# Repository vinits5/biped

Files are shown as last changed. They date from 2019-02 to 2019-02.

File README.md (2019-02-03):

# Biped Project

## Biped Assembly

It contains all the SolidWork parts for Biped Robot along with its Assembly.
<p float="center">
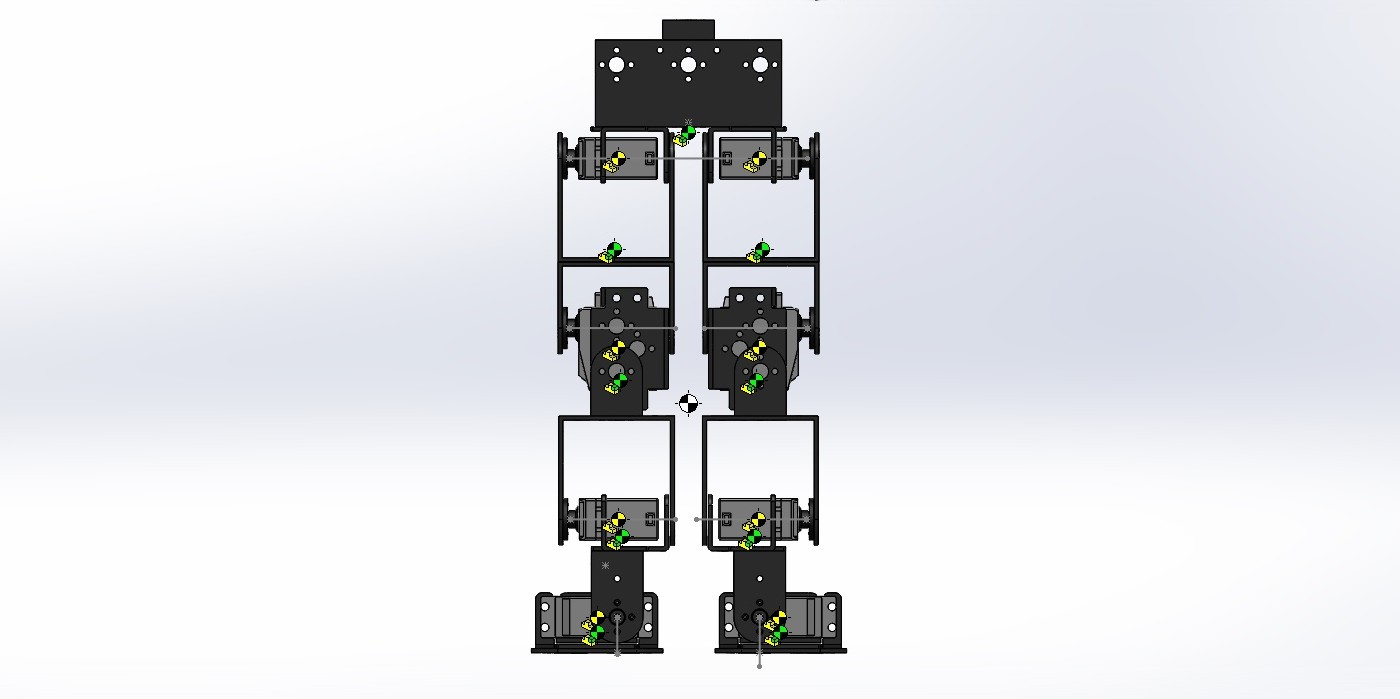
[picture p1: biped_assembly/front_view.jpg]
Front View of Assembly
	
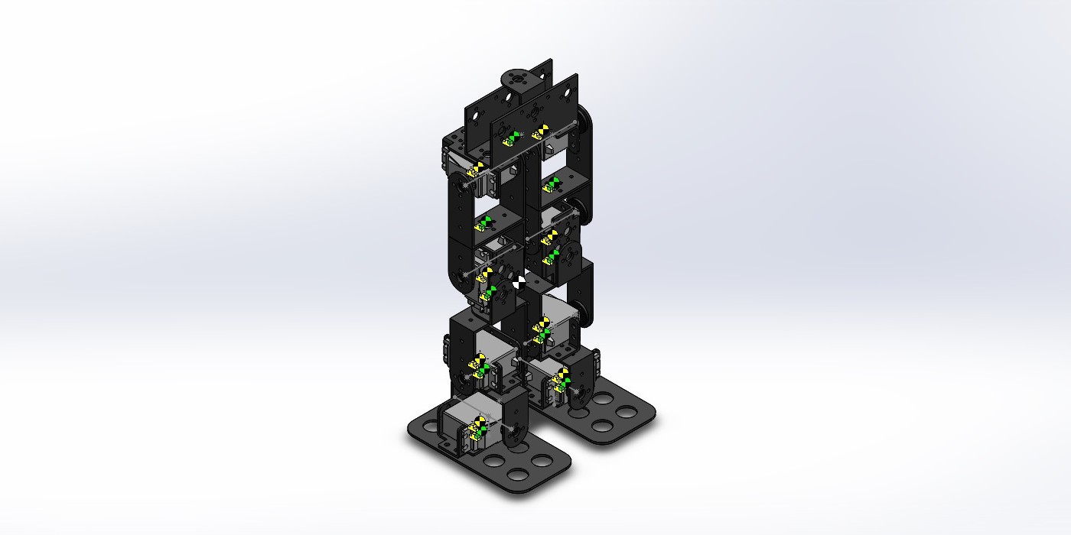
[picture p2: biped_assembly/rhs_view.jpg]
Right Hand Side View
	
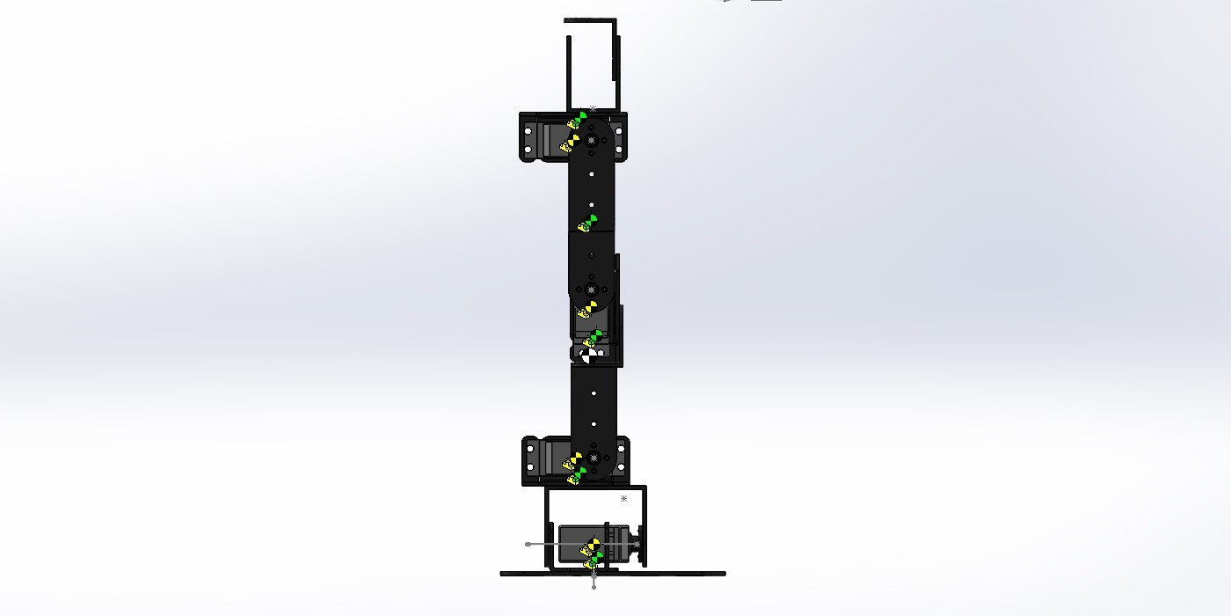
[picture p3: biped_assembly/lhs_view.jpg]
Left Hand Side View
	
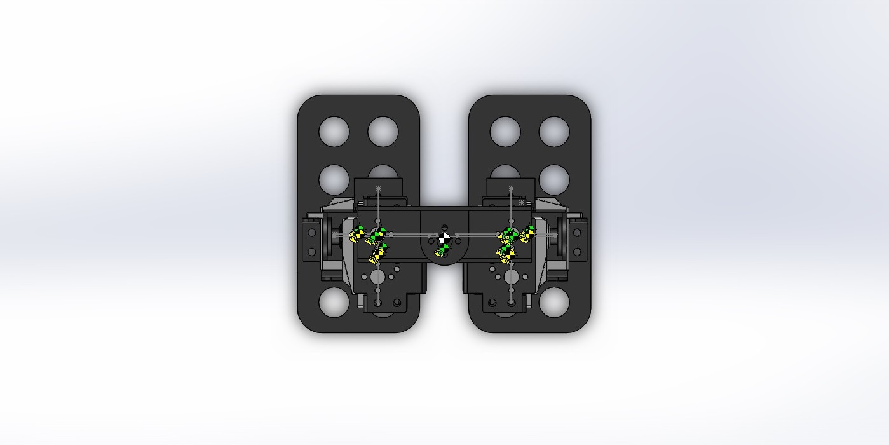
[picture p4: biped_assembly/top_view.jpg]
Top View
	
</p>

### Rendered Assembly
<p align="center">
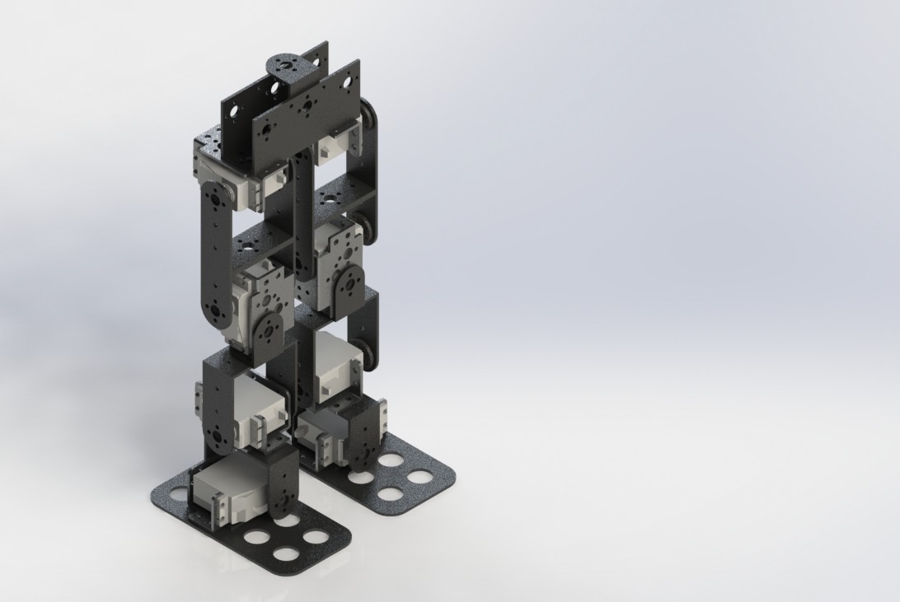
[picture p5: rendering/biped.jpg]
Rendered Biped
	
</p>

### Simulink Simulation
<p align="center">
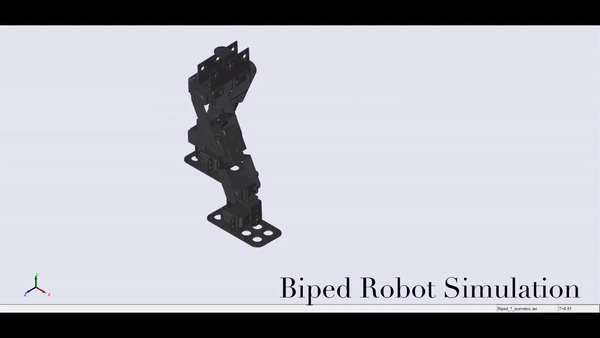
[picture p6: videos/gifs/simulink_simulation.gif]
	
</p>

## Robot

<p align="center">
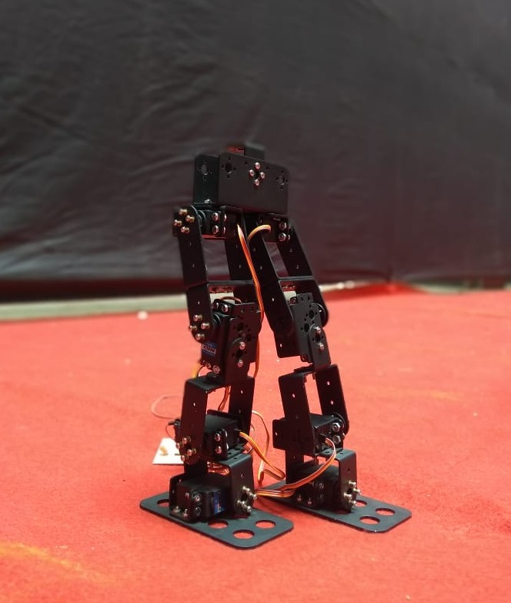
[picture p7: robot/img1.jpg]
	
</p>

<p align="center">
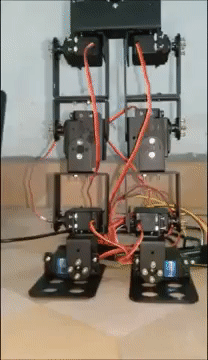
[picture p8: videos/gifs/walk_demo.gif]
	
</p>

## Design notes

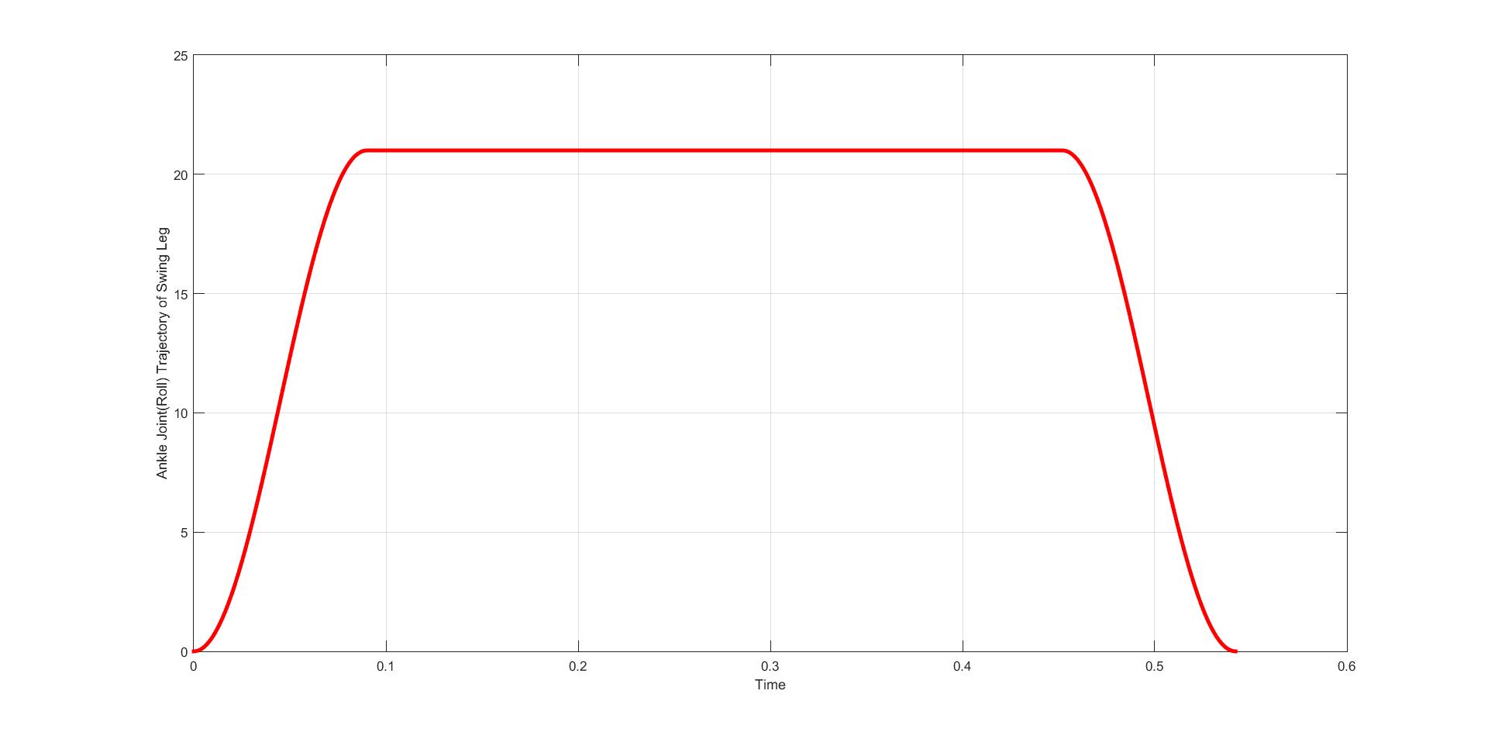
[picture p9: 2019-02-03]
biped_gait/Swing Ankle Roll.jpg

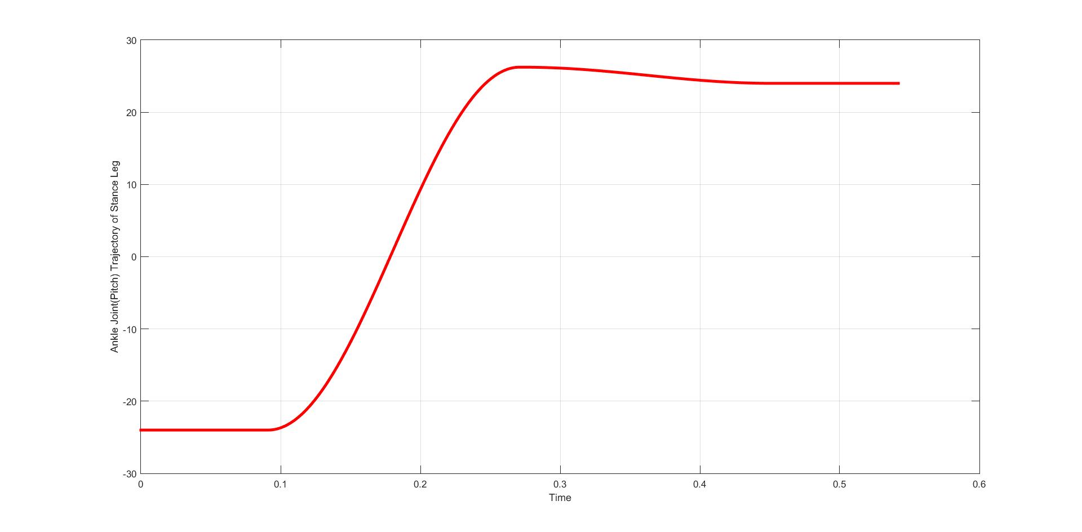
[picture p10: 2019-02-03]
biped_gait/Stance Ankle Pitch.jpg

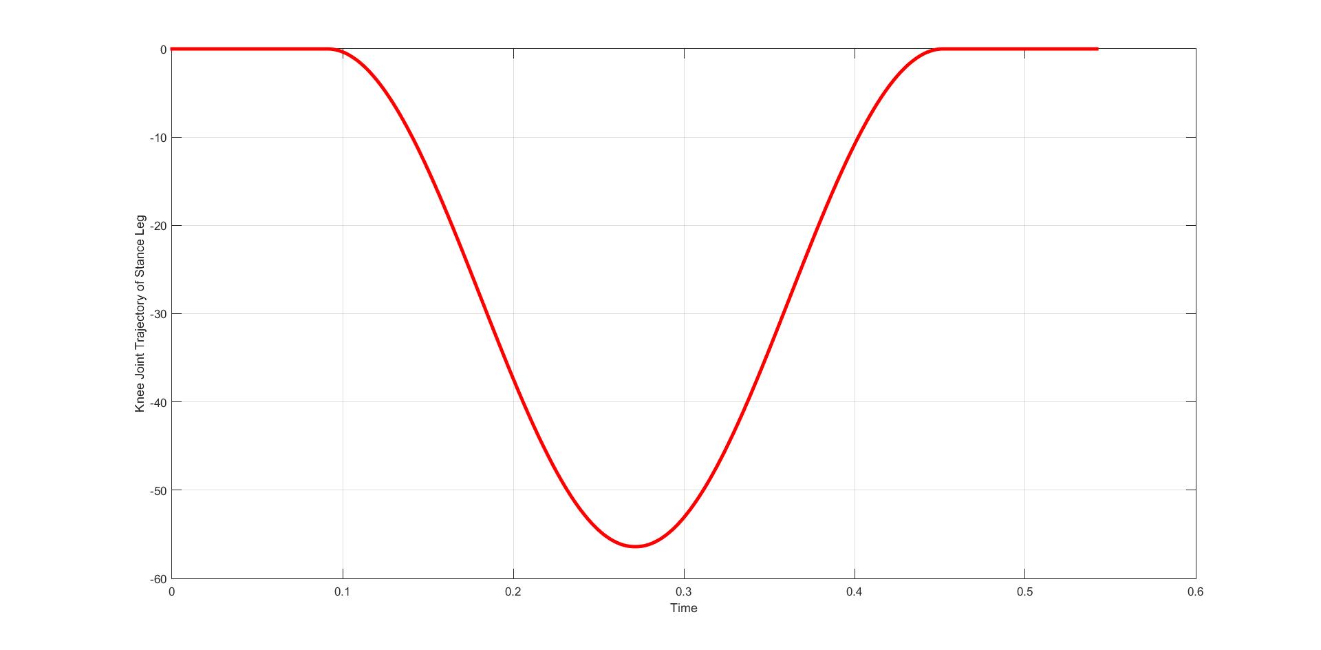
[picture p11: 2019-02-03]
biped_gait/Stance Knee.jpg

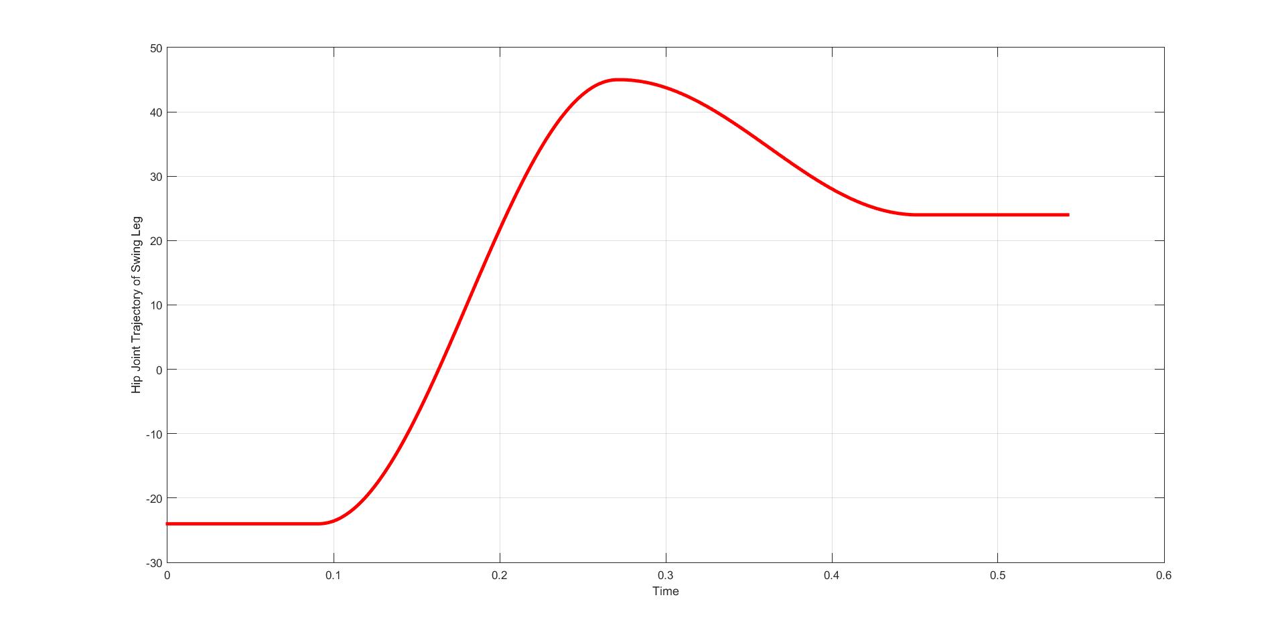
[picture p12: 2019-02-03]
biped_gait/Swing Hip.jpg

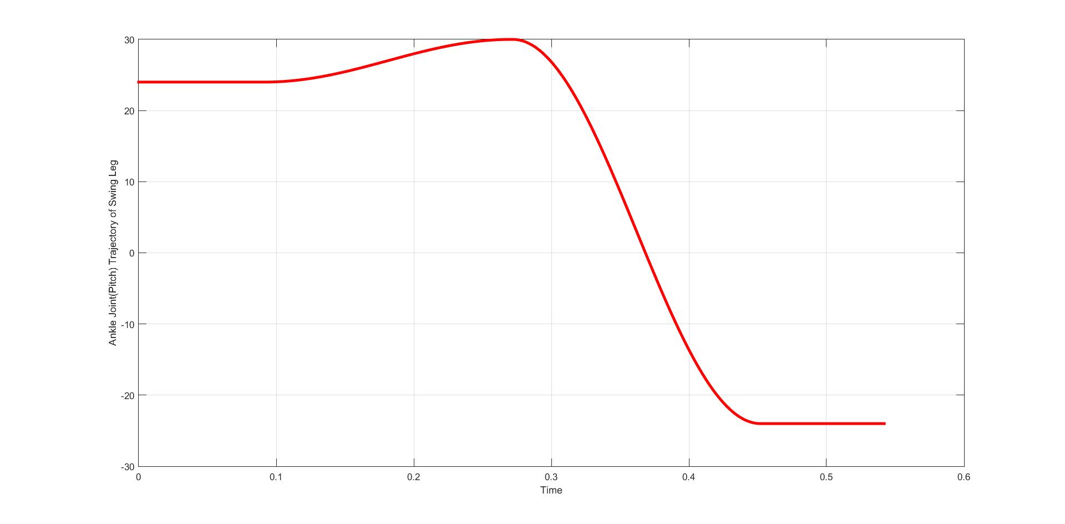
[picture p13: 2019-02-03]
biped_gait/Swing Ankle Pitch.jpg

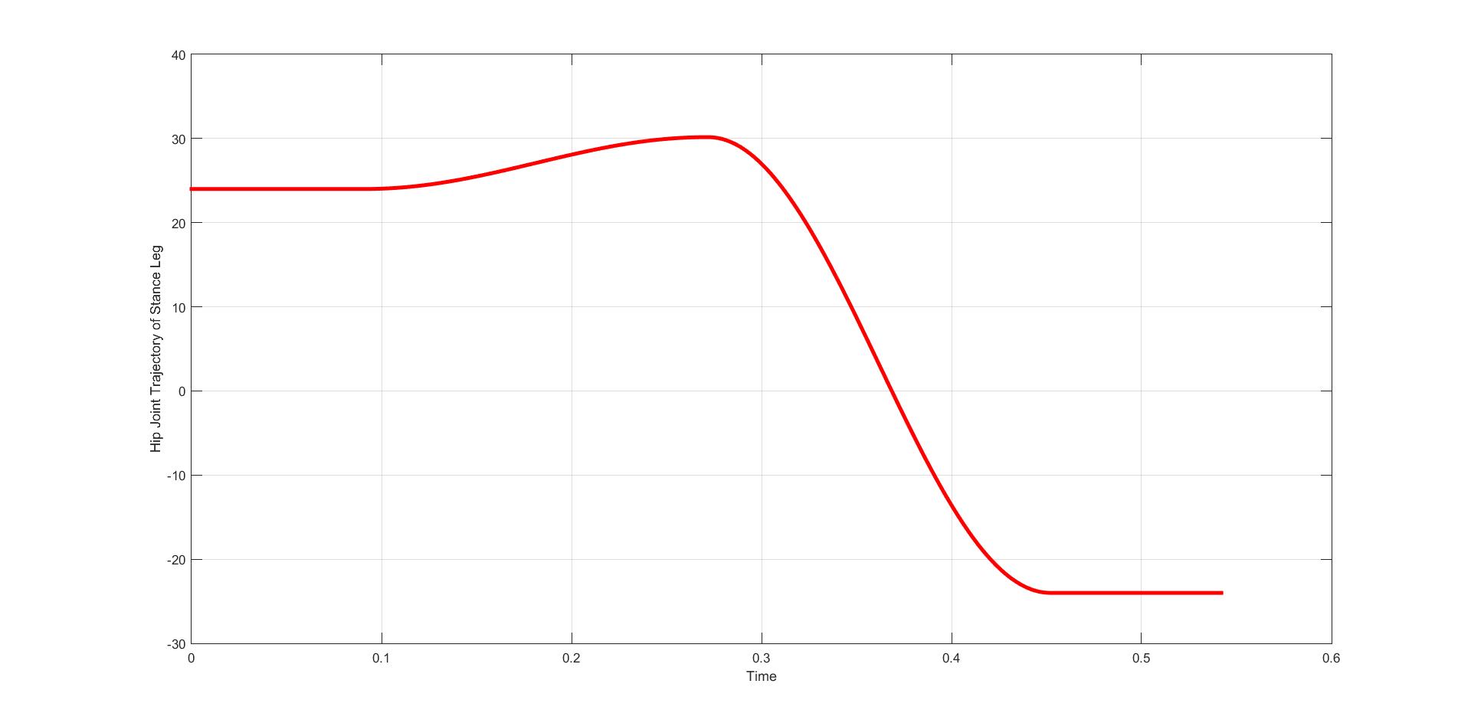
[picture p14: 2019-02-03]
biped_gait/Stance Hip.jpg

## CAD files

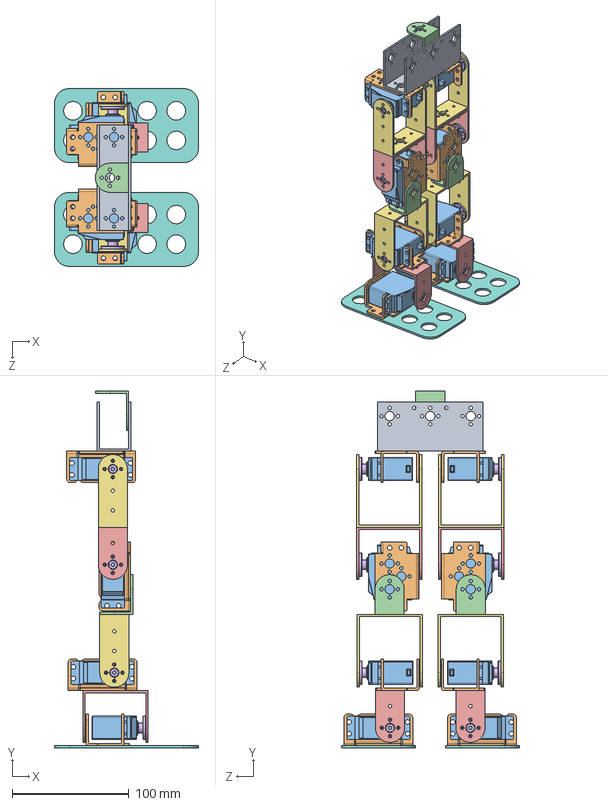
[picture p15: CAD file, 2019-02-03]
biped_assembly/Biped.SLDASM
123.4 x 305.8 x 152.4 mm
LARGE_U_BEAM_ALUMINIUM_SERVO_BRACKET
MULTIPURPOSE_Bracket x 8
Futaba_Servo_Motor x 8
L_SHAPED_INTERCONNECT_SERVO_BRACKET x 3
SHORT_U_SHAPE_ALUMINIUM_BRACKET x 4
Servo_Horn x 8
LONG_U_SHAPE_ALUMINIUM_BRACKET x 4
ROBOT_FEER_ALUMINIUM_SERVO_BRACKET x 2

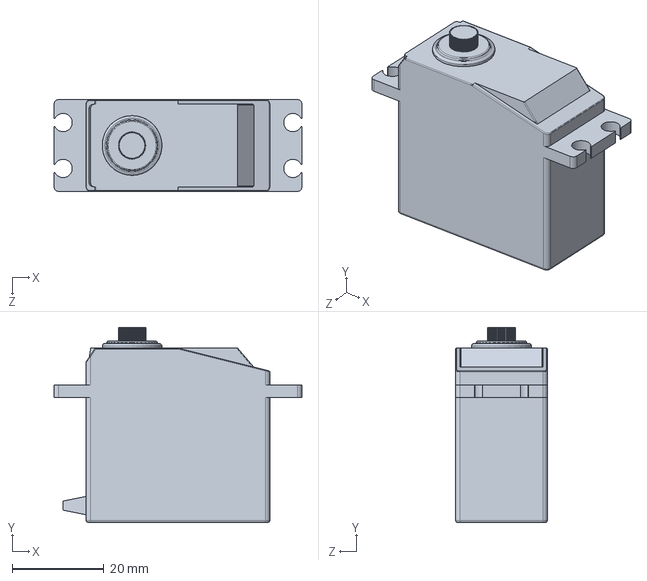
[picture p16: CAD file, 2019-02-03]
biped_assembly/Futaba_Servo_Motor.SLDPRT
54.0 x 42.5 x 20.0 mm

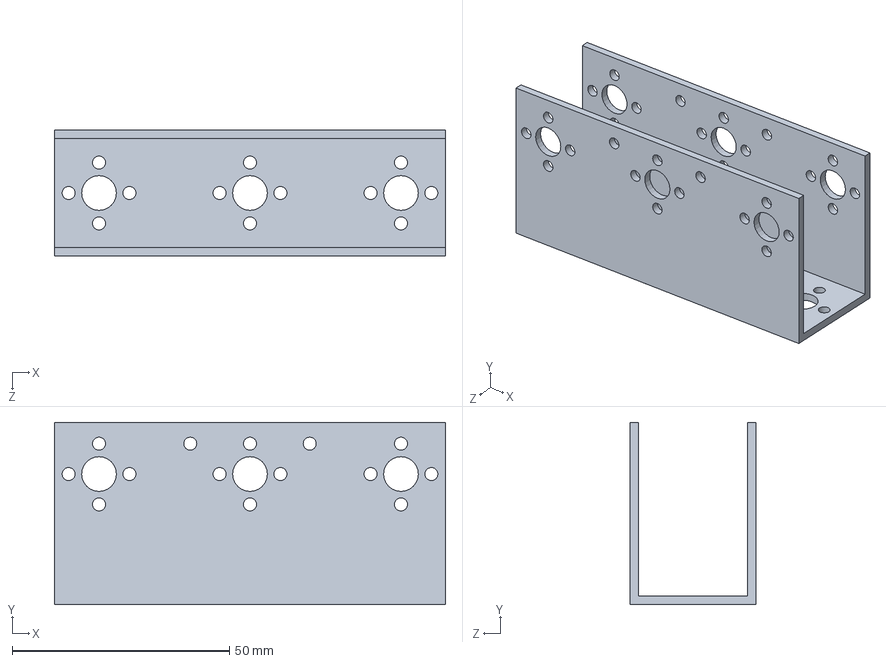
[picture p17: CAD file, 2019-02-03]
biped_assembly/LARGE_U_BEAM_ALUMINIUM_SERVO_BRACKET.SLDPRT
90.0 x 42.0 x 29.0 mm

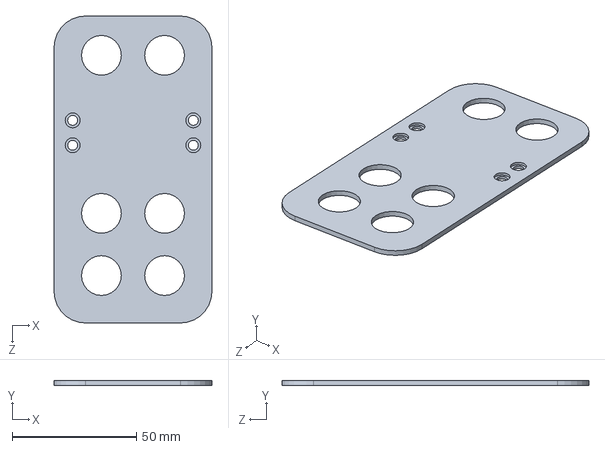
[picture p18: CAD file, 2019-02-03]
biped_assembly/ROBOT_FEER_ALUMINIUM_SERVO_BRACKET.SLDPRT
63.5 x 2.00 x 123.4 mm

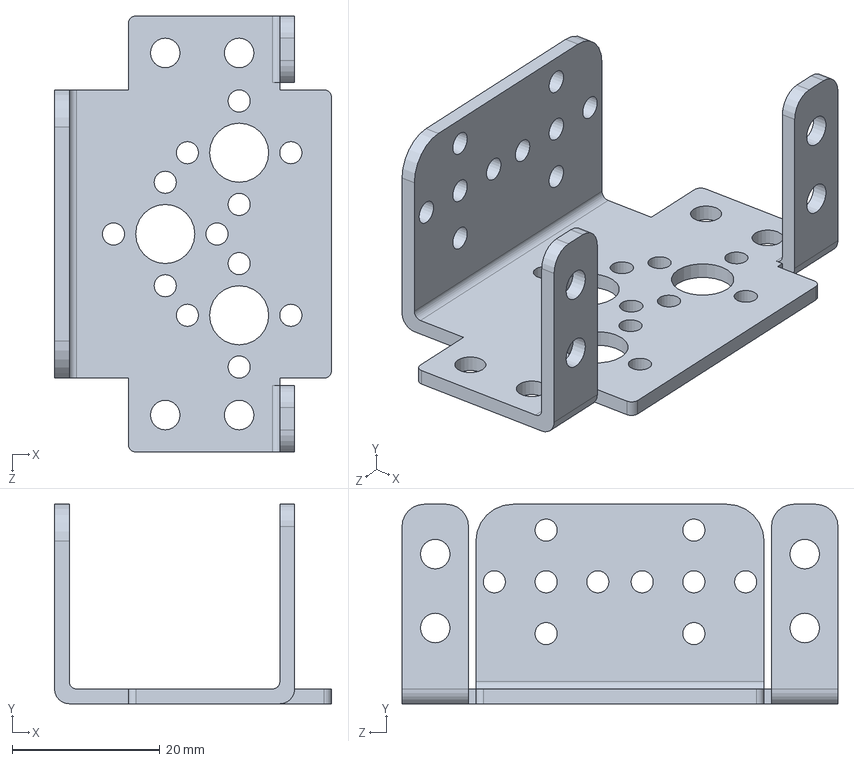
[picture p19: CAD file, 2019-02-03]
biped_assembly/MULTIPURPOSE_Bracket.SLDPRT
37.5 x 27.0 x 59.0 mm

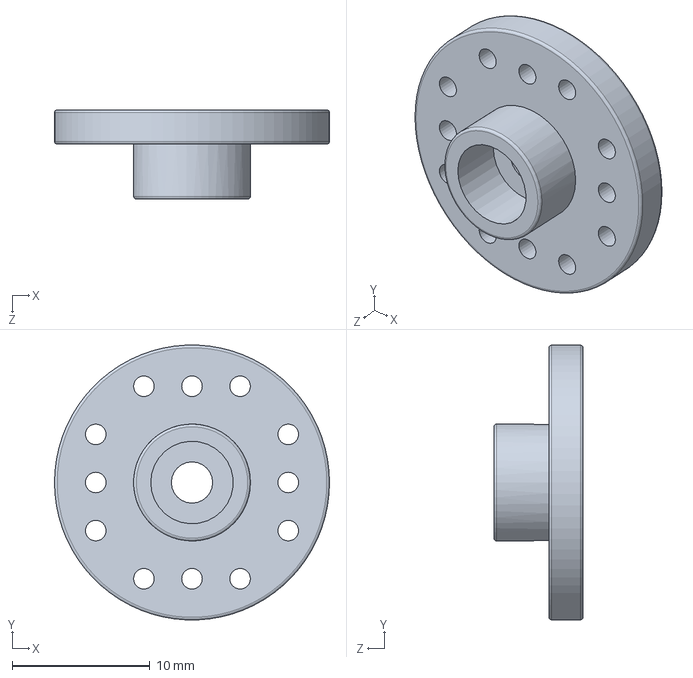
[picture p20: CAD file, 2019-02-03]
biped_assembly/Servo_Horn.SLDPRT
20.0 x 20.0 x 6.50 mm

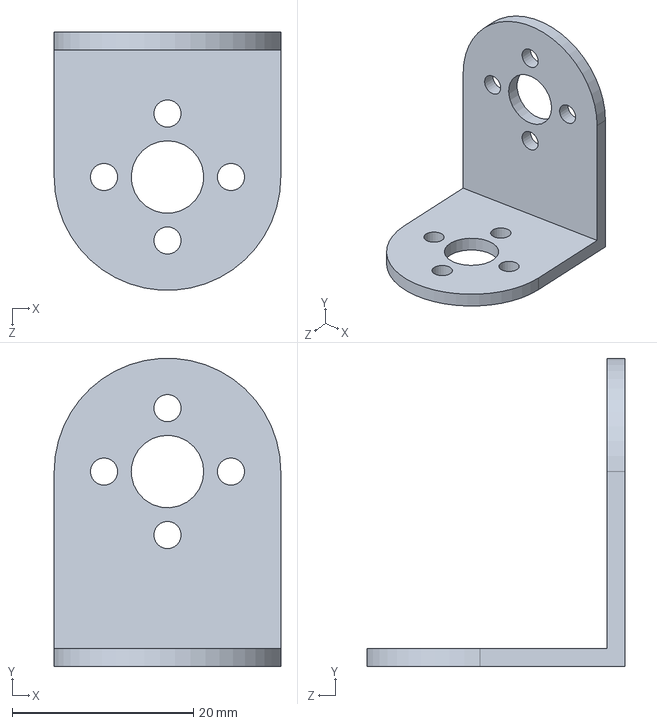
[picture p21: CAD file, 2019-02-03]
biped_assembly/L_SHAPED_INTERCONNECT_SERVO_BRACKET.SLDPRT
25.0 x 34.0 x 28.5 mm

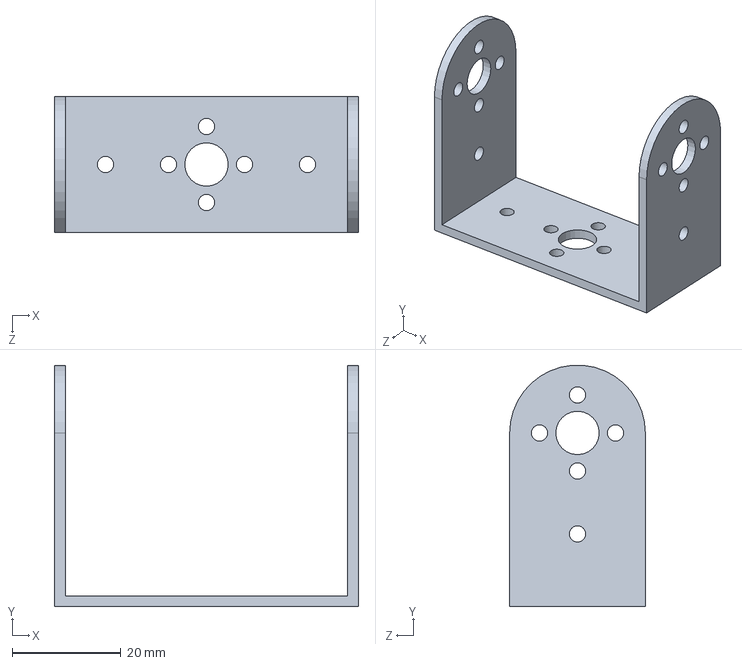
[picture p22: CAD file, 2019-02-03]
biped_assembly/SHORT_U_SHAPE_ALUMINIUM_BRACKET.SLDPRT
56.0 x 44.5 x 25.0 mm

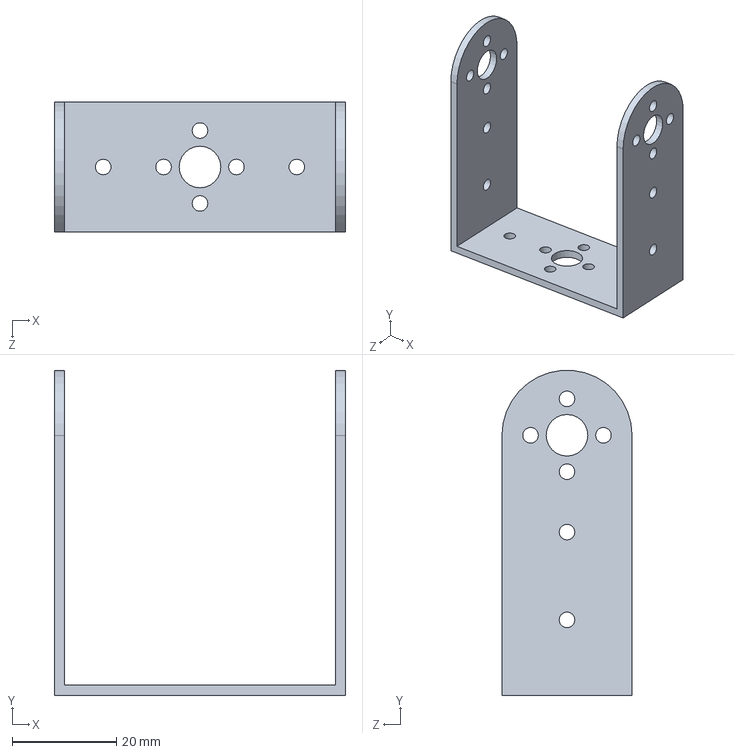
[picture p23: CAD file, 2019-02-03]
biped_assembly/LONG_U_SHAPE_ALUMINIUM_BRACKET.SLDPRT
56.0 x 62.4 x 25.0 mm

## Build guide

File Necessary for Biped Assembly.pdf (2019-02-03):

Created by Cytron Technologies Sdn. Bhd. – All Rights Reserved | 1

### OVERVIEW

This document describes the development of Cytron Technologies DIY (Do It Yourself) Project No.18 (PR18). This project will use PIC16F876A to communicate with Cytron SC16A servo controller to control the biped that built up with Cytron servo motors and servo brackets. It provides a LCD to display the information. Circuit schematic diagram and sample PIC source code are provided. Source code provides a simple biped walking program and servo position calibrating function.

PR18

### FEATURES

Basic Circuit
- PIC16F876A microcontroller
- Onboard 5V high current supply for SC16A
- Protection against overload (3A fuse)
- LCD screen display

SC16A Servo Controller
- Provides up to 16 control channels
- Simple communication protocol with UART

Biped
- 6 Cytron C40R servo motors
- 8 Cytron HD-SB-SH servo holders
- 6 Cytron U-Joints for servo motor

# Walking with Cytron Servo Motor

# Version 1.0

## August 2008

Cytron Technologies Sdn. Bhd.

Information contained in this publication regarding device applications and the like is intended through suggestion only and may be superseded by updates. It is your responsibility to ensure that your application meets with your specifications. No representation or warranty is given and no liability is assumed by Cytron Technologies Incorporated with respect to the accuracy or use of such information or infringement of patents or other intellectual property rights arising from such use or otherwise. Use of Cytron Technologies’s products as critical components in life support systems is not authorized except with express written approval by Cytron Technologies. No licenses are conveyed, implicitly or otherwise, under any intellectual property rights.

ROBOT . HEAD to TOE
PR18 – Walking With Cytron Servo Motor

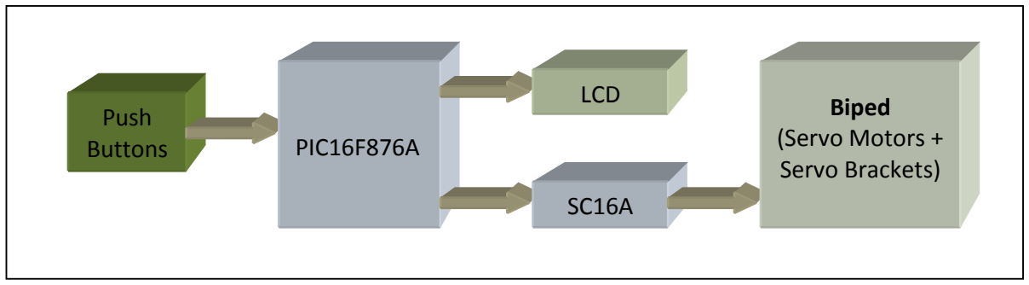
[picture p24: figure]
Push; Buttons; PIC16F876A; LCD; Biped (Servo Motors + Servo Brackets)

Created by Cytron Technologies Sdn. Bhd. – All Rights Reserved | 1

### SYSTEM OVERVIEW

### GENERAL DESCRIPTION

This project uses SC16A servo controller to control a servo biped. SC16A provides up to 16 control channels. PIC MCU communicates with the SC16A to transfer required data. The control of each servo motor will be stored in PIC MCU and displayed on LCD.

### PIC16F876A

This powerful (200 nanosecond instruction execution) yet easy-to-program (only 35 single word instructions) CMOS FLASH-based 8-bit microcontroller packs Microchip's powerful PIC® architecture into an 28-pin package and is upwards compatible with the PIC16C5X, PIC12CXXX and PIC16C7X devices. Feature of the device:
- 256 bytes of EEPROM data memory
- Self programming
- ICD (In Circuit Debugging function)
- 2 Comparators
- 5 channels of 10-bit Analog-to-Digital (A/D) converter
- 2 capture/compare/PWM functions
- the synchronous serial port can be configured as either 3-wire Serial Peripheral Interface (SPI™) or the 2-wire Inter-Integrated Circuit (I²C™) bus
- Universal | Asynchronous | Receiver
Transmitter (USART)

Figure 1
Figure 1 shows the pin diagram of the PIC16F876A. For more detail, please download the datasheet from microchip web site at: http://www.microchip.com

### SC16A

Figure 2
The SC16A servo controller offers up to 16 control channels. It can be daisy chained with another SC16A to provide total of 32 control channels. It uses UART interface to communicate with host microcontroller. It also provides communication with computer through USB port. Software is provided for computer to communicate with SC16A. The power sources for the servo motors and circuit are separated to provide more stable operation. For further information about SC16A, please refer to SC16A user manual from Cytron Technologies which can be downloaded from the link below:
http://www.cytron.com.my/datasheet/SC16A_User%27s_Manual_v1.pdf

### HARDWARE

This project will require following hardware:
a. 1 x PIC16F876A
b. 1 x PR18 Printed Circuit Board (PCB)
c. 1 x SC16A Servo Controller
d. 1 x 2X16 LCD
e. 6 x C40R Servo Motors
f. 8 x HD-SB-SH Servo Motor Holder
g. 6 x U-Joint for Servo Motor
h. Related hardware components
i. Related electronic components

Please refer to the schematic diagram of PR18. The schematic is provided free therefore Cytron Technologies will not be responsible for any further modification or improvement.

Created by Cytron Technologies Sdn. Bhd. – All Rights Reserved | 2

### Interface PIC16F876A with SC16A

Servo Power Supply

Servo Motor Ports | To PIC16F876A
Figure 3
SC16A servo controller provides UART interface which consists of 4 pins. The RX pin is connected to PIC16F876A’s TX (RC6) pin, whereas TX pin is connected to PIC16F876A’s RX (RC7) pin. The GND pin is connected to ground and 5V pin is connected to 5V. The PR18 PCB provides a high current power supply that can be connected to the servo power supply pins.

Figure 4 and figure 5 show the connection of UART interface between PR18 circuit board and SC16A.

Figure 4

Figure 5

Figure 6 and figure 7 show the connection of power supply from PR18 circuit board to SC16A.

Figure 6

Figure 7
Refer to Appendix A, the figure named PCB Layout (Completed with SC16A) shows the connection of SC16A and PR18 circuit board.

### Interface SC16A with servo motors

Figure 8 shows the connection of servo motor to SC16A. For Cytron C40S servo motor, the black pin is ground (-), red pin is positive power (+), and white pin is signal (s).

Figure 8

Created by Cytron Technologies Sdn. Bhd. – All Rights Reserved | 3 Vss 1 Vcc 2 Vee 3 RS ⁴ R/W ⁵

### Interface PIC16F876A with LCD (2X16 character)

To use the LCD, user has to solder 16 pin header pin to the LCD. LCD used in this project is JHD162A, for other type of LCD, please refer to its data sheet.

Figure 9

Figure 10
Figure 9 is a 2X16 character LCD. LCD connection pins and function of each pin are shown in table below:
Pin | Name | Pin function | Connection
1 | VSS | Ground | GND
2 | VCC | Positive supply for LCD | 5V
3 | VEE | Brightness adjust | RC2
4 | RS | Select register, select instruction or data register | RC3
5 | R/W | Select read or write | RC4
6 | E | Start data read or write | RC5
7 | DB0 | Data bus pin | RB0
8 | DB1 | Data bus pin | RB1
9 | DB2 | Data bus pin | RB2
10 | DB3 | Data bus pin | RB3
11 | DB4 | Data bus pin | RB4
12 | DB5 | Data bus pin | RB5
13 | DB6 | Data bus pin | RB6
14 | DB7 | Data bus pin | RB7
15 | LED+ | Backlight positive input | RC1
16 | LED- | Backlight negative input | GND

### Power supply for the circuit and SC16A

1

2

3

J1

PWR2.5

2

3

1

S1

SW-slide | C1 16V 100uF

100pF

C4
C CAP
100pF

C5
C CAP

IN 1
GND 2

OUT 3

LM7805

LM7805

C2
16V 100uF

LED
LED3mm

330

R1
Resistor
D1 | VCC

1N4007

2

3

1

S2

SW-toggle-H

18

R2

Resistor
C3

FUSE

3A Fuse

IN 3
GND 2

OUT 1

U2

LM78L05

Q1 TIP2955

1
2

JP2

3961-02H

1

2

JP1

Terminal Component

Figure 11
User can choose either to use the AC to DC adaptor (not included in the DIY project) or 7.4V-12V battery (not included in the DIY project) to power up the circuit. Higher input voltage will produce more heat at LM7805 voltage regulator. Typical voltage is 12V. Anyhow, LM7805 will still generate some heat at 12V. There are two type of power connector for the circuit, DC plug (J1) and Pluggable Terminal Block (JP1). Normally AC to DC adaptor can be plugged to J1 type connector. Shown in Figure 11, the D1 is use to protect the circuit from wrong polarity supply. C1 and C4 are for stabilizing the voltage at the input side of the LM7805 voltage regulator, while the C2 and C5 are for stabilizing the voltage at the output side of the LM7805 voltage supply. The “LED” is green LED to indicate the power status of the circuit. R1 is resistor to protect LED from over current that will burn the LED. C3 is used to stabilize the voltage at the input side of LM78L05. LM78L05 provides reference voltage for TIP2955 to supply high current 5V source and LM78L05 consumes very low power. Heat sink is required by TIP2955 to supply high current as it produces a lot of heat while operating. The fuse ensures the maximum current flow (3A) is not exceeded. The output of the TIP2955 is connected to 3961-02-H (JP2). It can be connected to SC16A to supply power. A low voltage power supply to the whole circuit (>7V) can reduce the heat production on TIP2955. Typical 7.4V battery supply is strongly recommended.

Warning:Usual AC to DC adaptor does not support high current output (normally <500mA). If AC to DC adaptor is to be used, make sure it can supply high current (>2A).

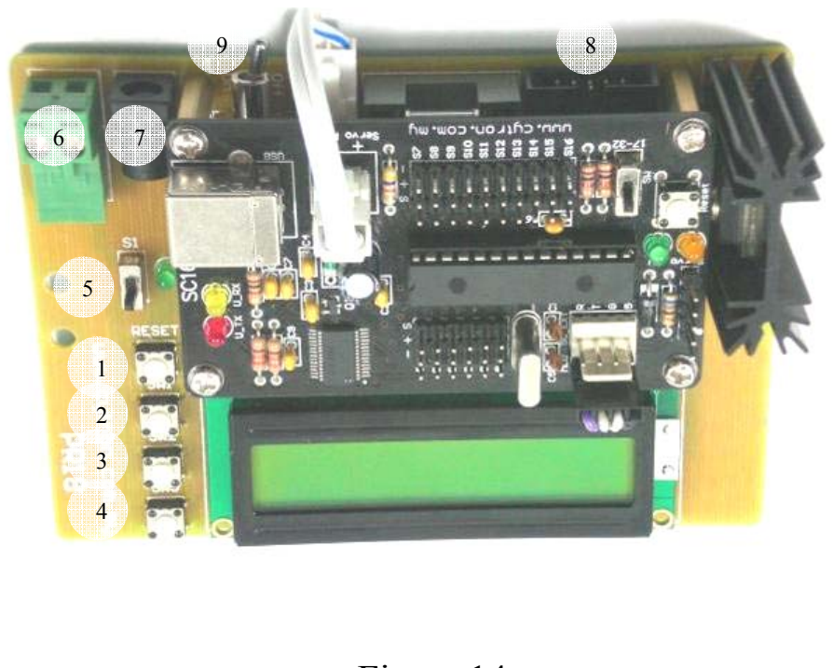
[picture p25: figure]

Created by Cytron Technologies Sdn. Bhd. – All Rights Reserved | 4
Push | Button | as | input | for | PIC

### microcontroller

RA0

SW1

10K

R4
Resistor

VCC

Figure 12
One I/O pin is needed for one push button as input of PIC microcontroller. The connection of the push button to the I/O pin is shown in Figure 12. The I/O pin should be pull up to 5V using a resistor (with value range 1K-10K) and this configuration will result an active-low input. When the button is being pressed, reading of I/O pin will be in logic 0, while when the button is not pressed, reading of that I/O pin will be logic 1.
ICSP | for | programming | PIC

### microcontroller

ICSP stands for In Circuit Serial Programming and describes the serial programming interface for PIC microcontroller. ICSP gives you a convenient way of programming PIC Microcontroller without removing the chip from the development or production board. All you need is a programmer that provides the ICSP connector.

MCLR
RB6
RB7
1 | 2
3 | 4
5 | 6
7 | 8
9 | 10

UIC00A

Header 5X2 -H
Figure 13

MCLR, RB6 and RB7 need to be connected to the USB In Circuit Programmer (UIC00A) to program the PIC microcontroller. The programmer (UIC00A) is not included in DIY project set since it can be used several time for different project set. User can also choose other type of PIC programmer to load the program.

For the instruction of using PIC programmer, please refer to the particular PIC programmer user’s manual.

### PCB circuit board

Figure 14
Component:
1. RESET button.
2. SW1 button.
3. SW2 button.
4. SW3 button.
5. S1 Slides switch (Circuit Power ON/OFF).
6. Power connector (7-12V).
7. DC plug socket (To 7-12V AC to DC adaptor).
8. Box header (To ICSP programmer).
9. S2 Toggle switch (Motor Power ON/OFF).

Please refer to Appendix A for the PCB layout of PR18. The PCB layout is provided free therefore Cytron Technologies will not be responsible for any further modification or improvement.

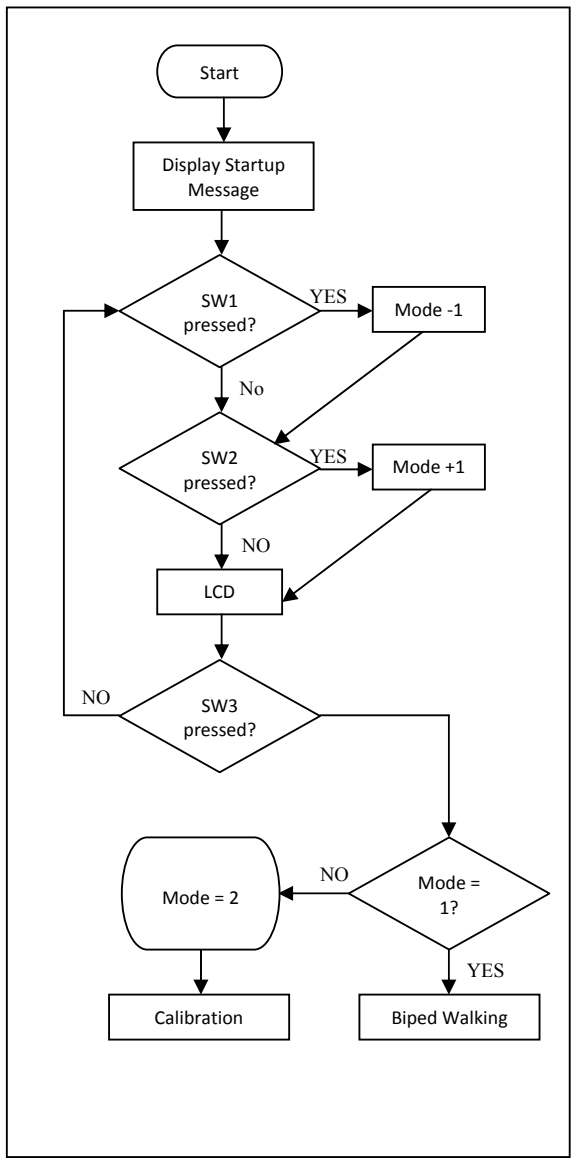
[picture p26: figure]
Start; Display Startup Message; SW1 pressed?; Biped Walking; LCD; SW2 pressed?; SW3 pressed?; Mode ‐1; Mode +1; YES; Mode = 1?; Calibration; Mode = 2

Created by Cytron Technologies Sdn. Bhd. – All Rights Reserved | 5

### SOFTWARE

### Flowchart:

### Program

Please download the sample program from Cytron website (same directory as this DIY project)

Figure 15 shows the configuration of each servo motors in the program. L1 refers to the servo motor that located at the top of biped’s left leg. L2 refers to the middle left servo motor and L3 refers to the bottom left servo motor. The value of L1, L2 and L3 (in hexadecimal format) refers to which channel the servo motor is connected to SC16A. (For more information. please refer to figure 88 under GETITNG START).

For the mid_LX (X = 1, 2, or 3), it is the middle position (about 90 degree) of the servo motor’s shaft. The same is applied to R1, R2 and R3. It needs to be calibrated for the exact middle position. Each servo motor has different value. The calibration procedures will be discussed in later topic. (Refer to Calibrate the Servo Motor’s Position under GETTING START).

Figure 15
For more information about the software for this system, please refer to the source code provided. The explanation of each instruction is provided in the source code as the comment of each line.

The source code is provided free and Cytron Technologies will not be responsible for any further modification or improvement.

### GETTING START The PR18 Circuit

User can obtain the hardware set for this project (PR18) either by online purchasing (www.cytron.com.my) or purchase it in Cytron Technologies Shop.
1. Once user has the hardware set, soldering process can be started. Please solder the electronic components one by one according the symbols or overlays on the Printed Circuit Board (PCB). Ensure the component value and polarity is correctly soldered. Please refer to PCB Layout in Appendix A.

Caution: Make sure all the connectors (2510, 3961) are soldered in proper side. Those electronic components have polarity such as capacitor, diode, PIC, LM7805, LM78L05, TIP2955 and LED should be soldered in right polarity or it may cause the circuit board fail to work.

Warning:Before the battery (Power) is plugged in, make sure the polarity is correct to prevent the explosion. Wrong polarity of capacitor also may cause explosion.

2. Create the connection cable for the SC16A servo controller.

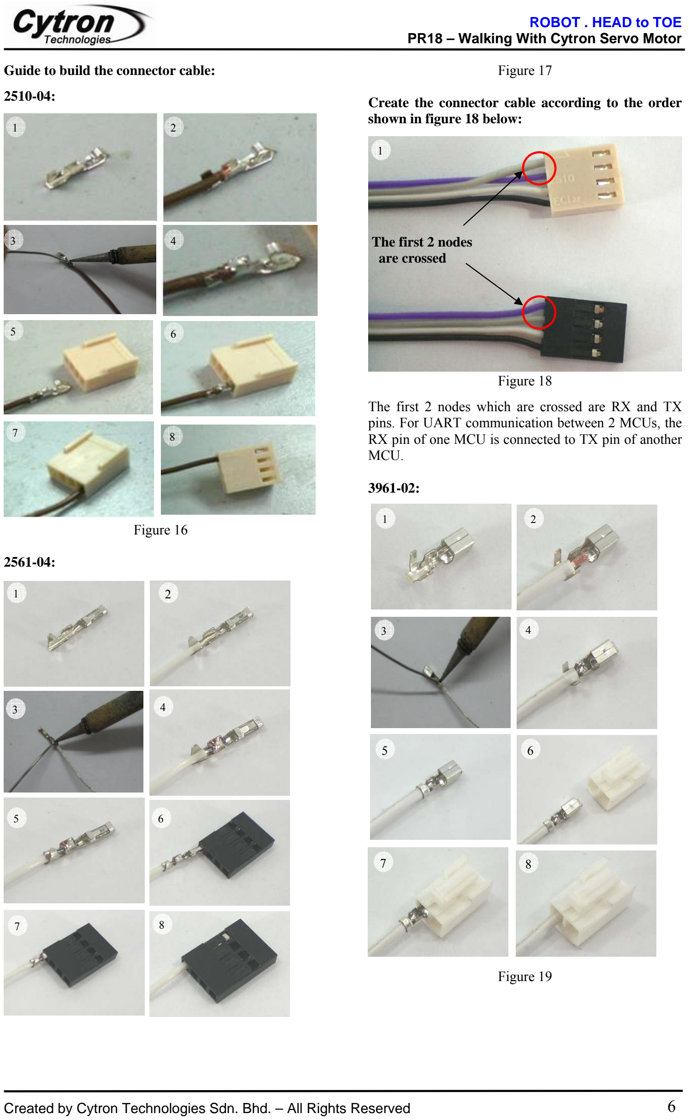
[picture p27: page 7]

Created by Cytron Technologies Sdn. Bhd. – All Rights Reserved | 6

Guide to build the connector cable: 2510-04:

Figure 16

2561-04:

Figure 17

Create the connector cable according to the order shown in figure 18 below:

The first 2 nodes
are crossed

Figure 18
The first 2 nodes which are crossed are RX and TX pins. For UART communication between 2 MCUs, the RX pin of one MCU is connected to TX pin of another MCU.

3961-02:

Figure 19

1

1 | 2
5 | 6

8 7

3 | 4

7

5 | 6
3 | 4
1 | 2

8

1 | 2

3

6

7

5

4

8

Created by Cytron Technologies Sdn. Bhd. – All Rights Reserved | 7

Create the connector cable according to the order shown in figure 20 below:

Figure 20
3. Assemble the TIP2955 transistor with heat sink.

Figure 21

4. Solder the TIP2955 with heat sink onto the PR18 Printed Circuit Board.
5. Mount the SC16A servo controller onto the Printed Circuit Board (Refer to figure 4, 5, 6, 7 and PCB Layout (Completed with SC16A) under Appendix A).
6. Connect the power supply to the circuit to terminal block or DC socket. For terminal block, please refer to the below figures.

Create the power supply to terminal block according to the order shown in figure 22 below:

Figure 22
7. Please download the necessary files and document from Cytron Technologies website. These included documentation, sample source code, schematic, component list and software.
8. The next step is to install MPLAB IDE and HI-TECC C PRO into a computer. The MPLAB IDE and HI-TECC C PRO can be downloaded from www.cytron.com.my . Please refer MPLAB IDE installation step document to install the software. The documents can be used to any version of MPLAB IDE software.
9. After the installation complete, open the project file provided using MPLAB IDE. Please refer MPLAB Open Project document to open the sample program.
10. Plug in power supply for the circuit. User can choose to use battery or AD to DC adaptor.
11. Build the project and load the hex file into the PIC microcontroller using the USB In Circuit Programmer (UIC00A). When user build the project, MPLAB IDE will generate hex file. The hex file generated from MPLAB IDE will be named according to project name, not C file name. Cytron Technologies also provide hex file for user. Do not forget to switch ON the power. The programmer is not included in the hardware set but it can be found at Cytron website. (User manual is provided at website).

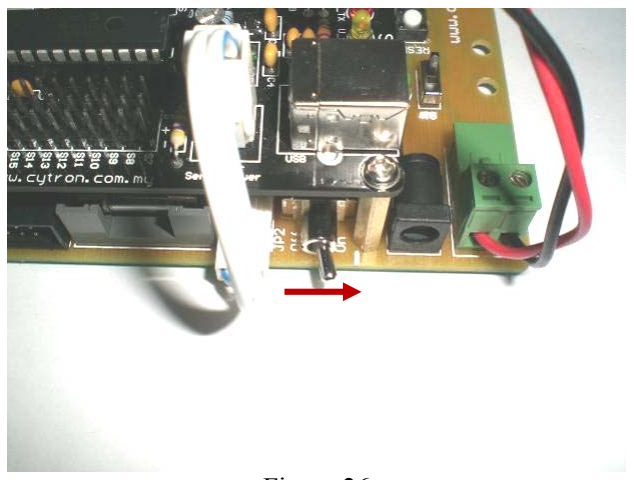
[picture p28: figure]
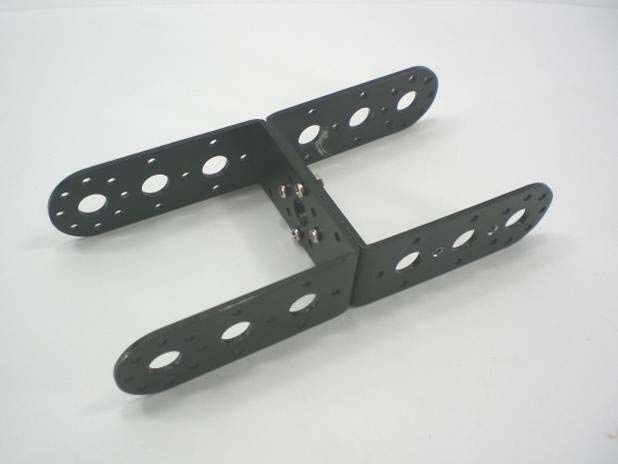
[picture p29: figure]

Created by Cytron Technologies Sdn. Bhd. – All Rights Reserved | 8
12. PIC is now completely programmed.
13. Proceed to “Set up Biped”.

### Set up Biped

The following steps refer to figure 23 below. This figure shows the bolts, nuts and screws that are available in the package of PR18.

Figure 23
Steps required when mating servo motor and its horn. (These are not the first steps but are the steps that will be referred in the later part.)
I. Connect the servo motor to the completed circuit (with programmed PIC with original program without modification) as shown in figure 24. The channel can be any from S7 to S12.

Figure 24
II. Turn on the S1 switch of the circuit as shown in figure 25.

Figure 25

III. Turn on the S2 switch of the circuit as shown in figure 26.

Figure 26
IV. The servo motor will turn to its default position (732). This position is about the middle position of the range that it able to turn.

Complete the biped
1. Prepare the components as shown in figure 27. 2 U joints and 4 sets of A screw.

Figure 27
2. Mate the joints with A screw sets. Refer to figure 28 until 30.

Figure 28

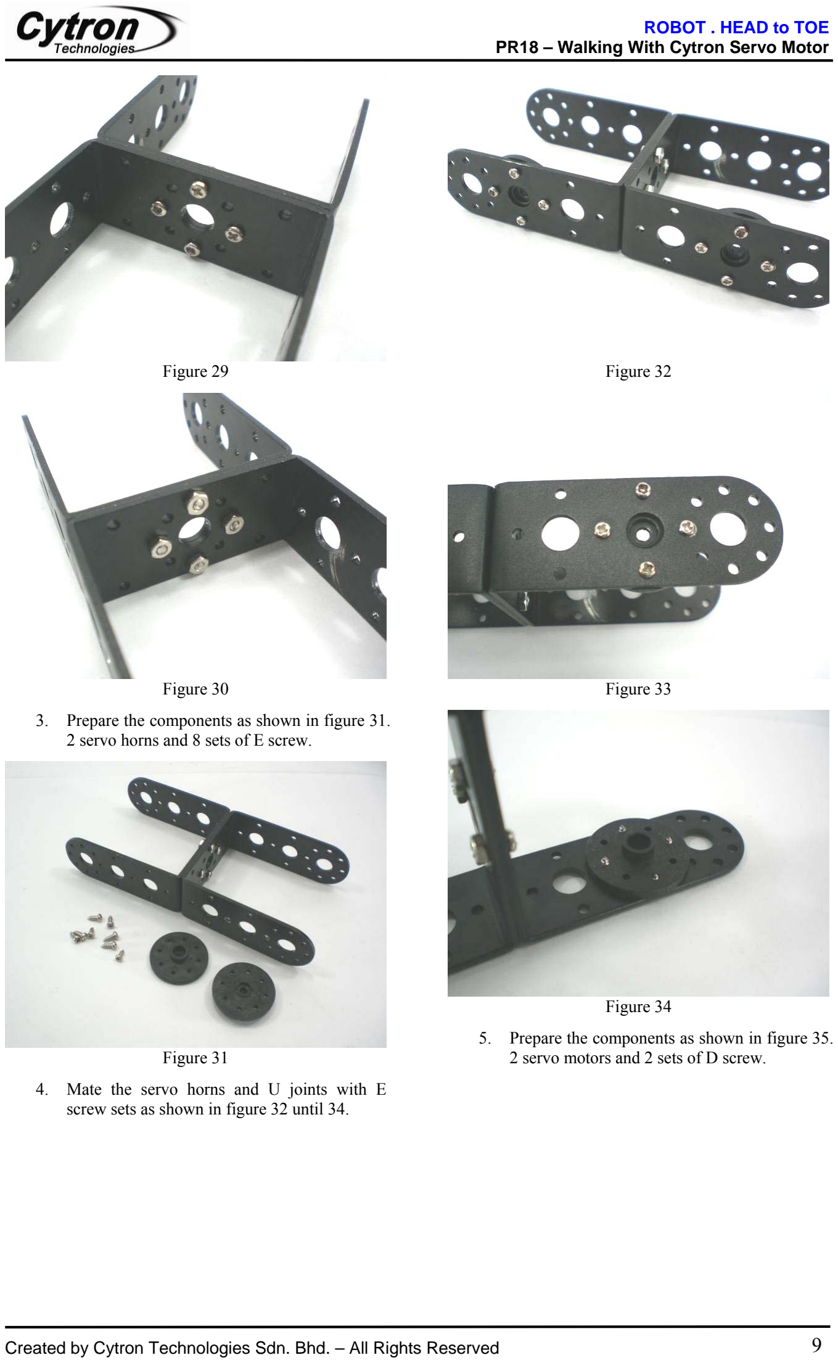
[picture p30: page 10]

Created by Cytron Technologies Sdn. Bhd. – All Rights Reserved | 9

Figure 29

Figure 30
3. Prepare the components as shown in figure 31. 2 servo horns and 8 sets of E screw.

Figure 31
4. Mate the servo horns and U joints with E screw sets as shown in figure 32 until 34.

Figure 32

Figure 33

Figure 34
5. Prepare the components as shown in figure 35. 2 servo motors and 2 sets of D screw.

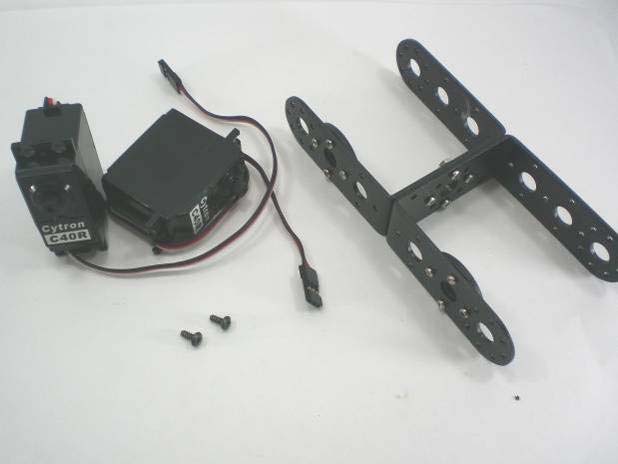
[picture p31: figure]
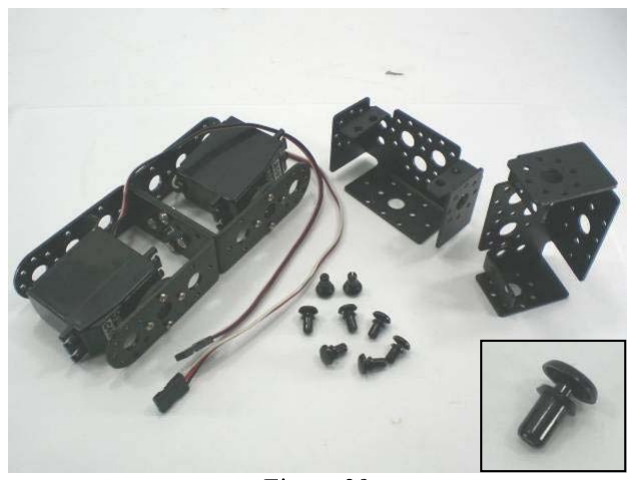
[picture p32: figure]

Created by Cytron Technologies Sdn. Bhd. – All Rights Reserved | 10

Figure 35
6. Refer to steps I - IV, mate the servo motors and its horns with D screw sets as shown in figure 36 until 38. The steps are required to ensure the servo motors are mated at the middle position of their moveable range. As shown in figure 36, a successful mating is defined by the servo motors are nearly parallel to the servo holder while the circuit and motors are turned on. The circuit can be turned off and the servo motors can be disconnected after mating. The topic “Calibrate the Servo Motor’s Position” discusses how to tune the motor to its exact middle position.

Figure 36

Figure 37

Figure 38
7. Prepare the components as shown in figure 39. 2 servo brackets, 8 servo rivets.

Figure 39
8. Mate the servo motors and brackets with servo rivets as shown in figure 40 until 43.

Figure 40

*While circuit and servo motor are turned on.

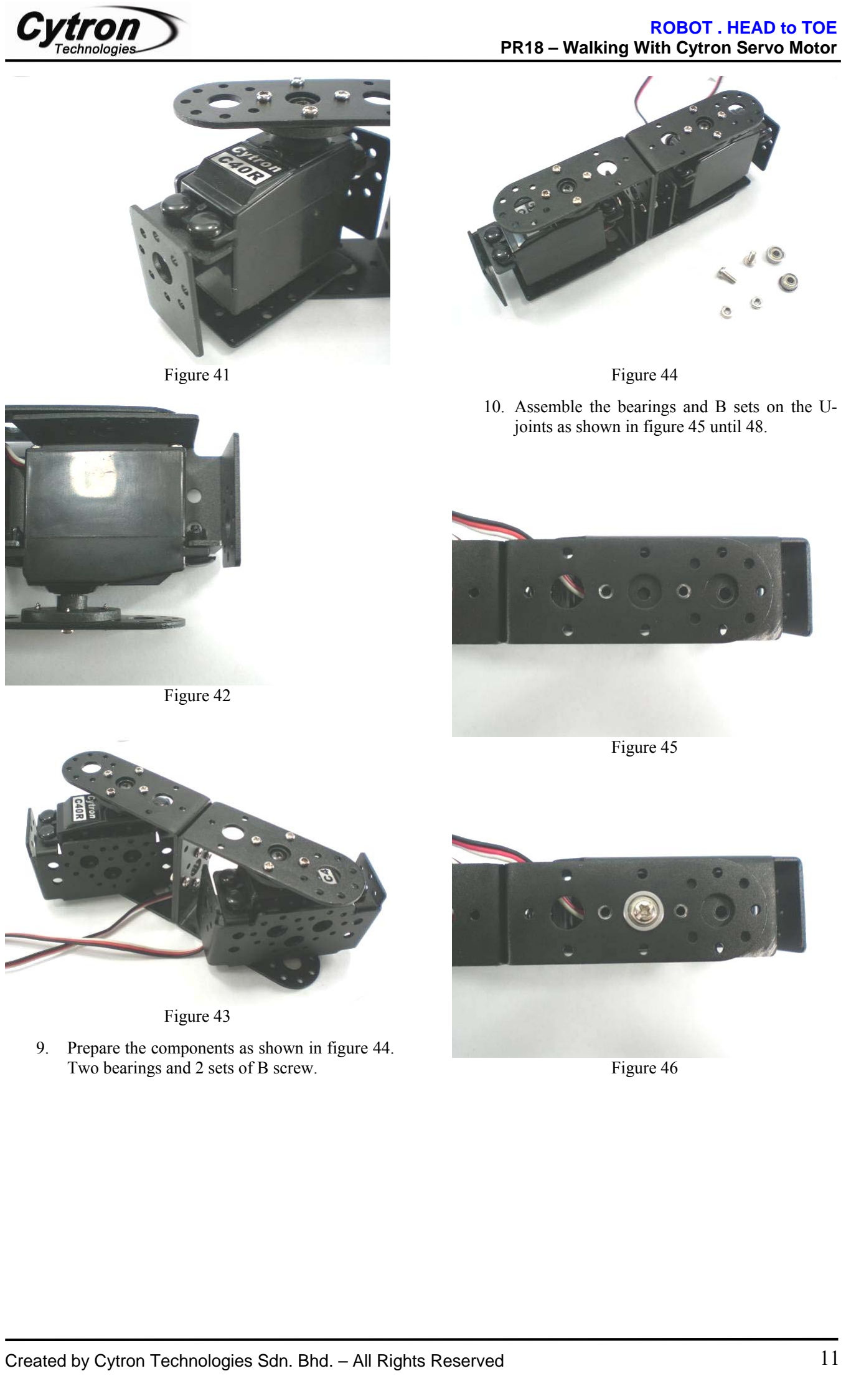
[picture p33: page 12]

Created by Cytron Technologies Sdn. Bhd. – All Rights Reserved | 11

Figure 41

Figure 42

Figure 43
9. Prepare the components as shown in figure 44. Two bearings and 2 sets of B screw.

Figure 44
10. Assemble the bearings and B sets on the U-joints as shown in figure 45 until 48.

Figure 45

Figure 46

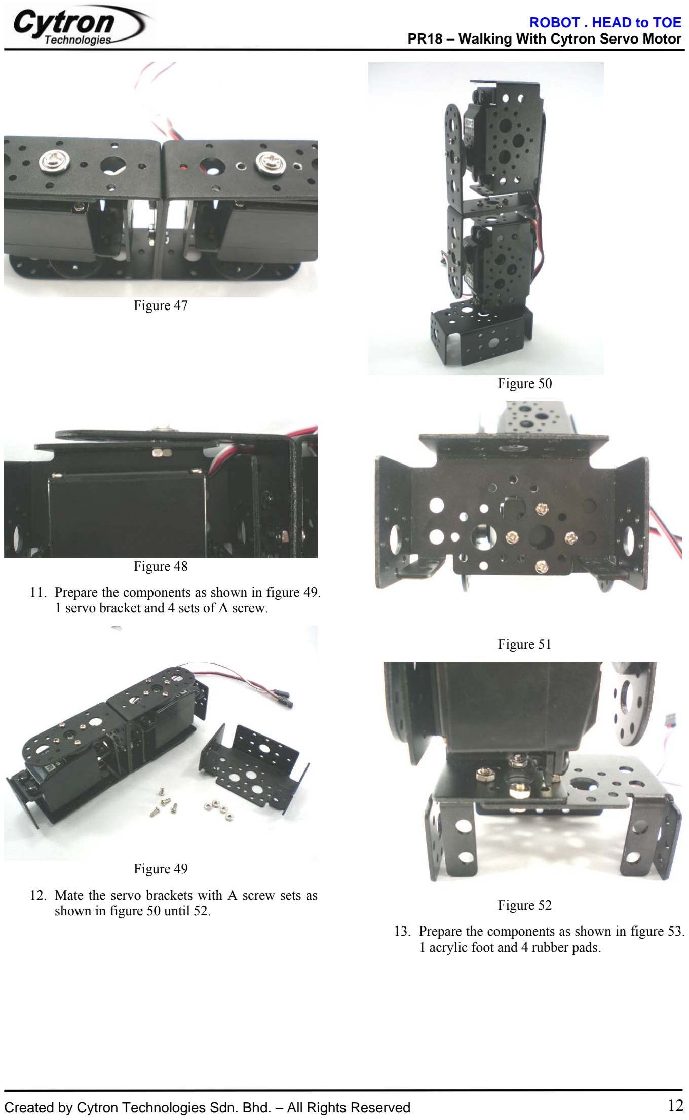
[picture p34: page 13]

Created by Cytron Technologies Sdn. Bhd. – All Rights Reserved | 12

Figure 47

Figure 48
11. Prepare the components as shown in figure 49. 1 servo bracket and 4 sets of A screw.

Figure 49
12. Mate the servo brackets with A screw sets as shown in figure 50 until 52.

Figure 50

Figure 51

Figure 52
13. Prepare the components as shown in figure 53. 1 acrylic foot and 4 rubber pads.

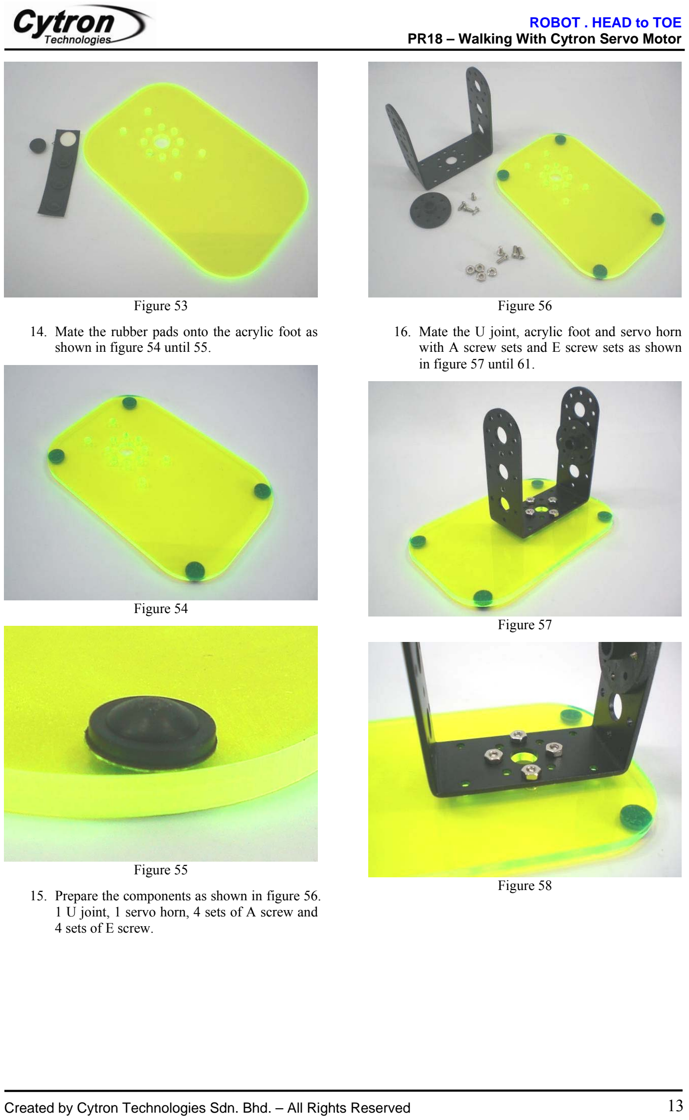
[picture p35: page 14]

Created by Cytron Technologies Sdn. Bhd. – All Rights Reserved | 13

Figure 53
14. Mate the rubber pads onto the acrylic foot as shown in figure 54 until 55.

Figure 54

Figure 55
15. Prepare the components as shown in figure 56. 1 U joint, 1 servo horn, 4 sets of A screw and 4 sets of E screw.

Figure 56
16. Mate the U joint, acrylic foot and servo horn with A screw sets and E screw sets as shown in figure 57 until 61.

Figure 57

Figure 58

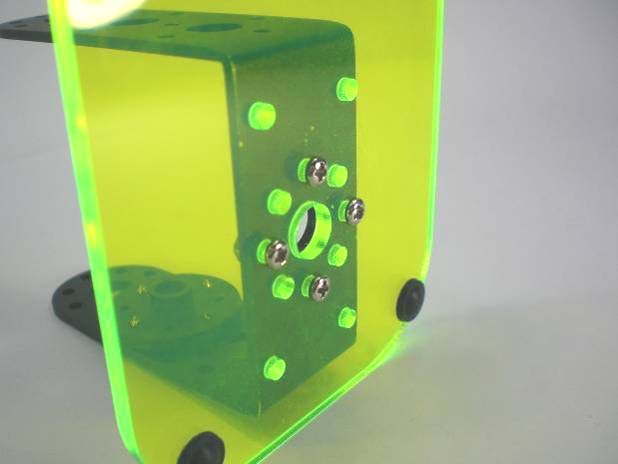
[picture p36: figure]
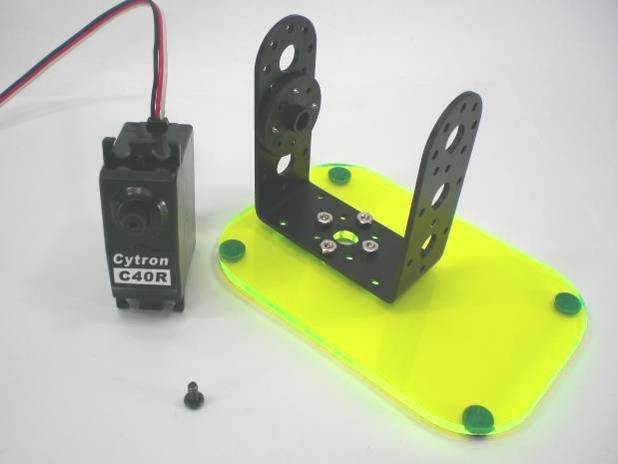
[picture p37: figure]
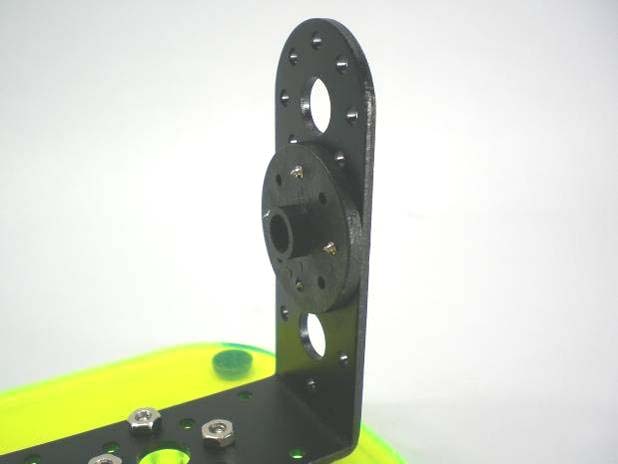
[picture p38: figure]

Created by Cytron Technologies Sdn. Bhd. – All Rights Reserved | 14

Figure 59

Figure 60

Figure 61
17. Prepare the components as shown in figure 62. 1 servo motor and 1 set of D screw.

Figure 62
18. Refers to steps I – IV, mate the servo motor and its horn with D set as shown in figure 63 until 66. As in step 6, the steps are required to ensure the servo motor is mated at the middle position of its moveable range. As shown in figure 66, a successful mating is defined by the servo motor is nearly perpendicular to the servo holder while the circuit and motor are turned on. The circuit can be turned off and the servo motor can be disconnected after mating. The topic “Calibrate the Servo Motor’s Position” discusses how to tune the motor to its exact middle position.

Figure 63

Figure 64

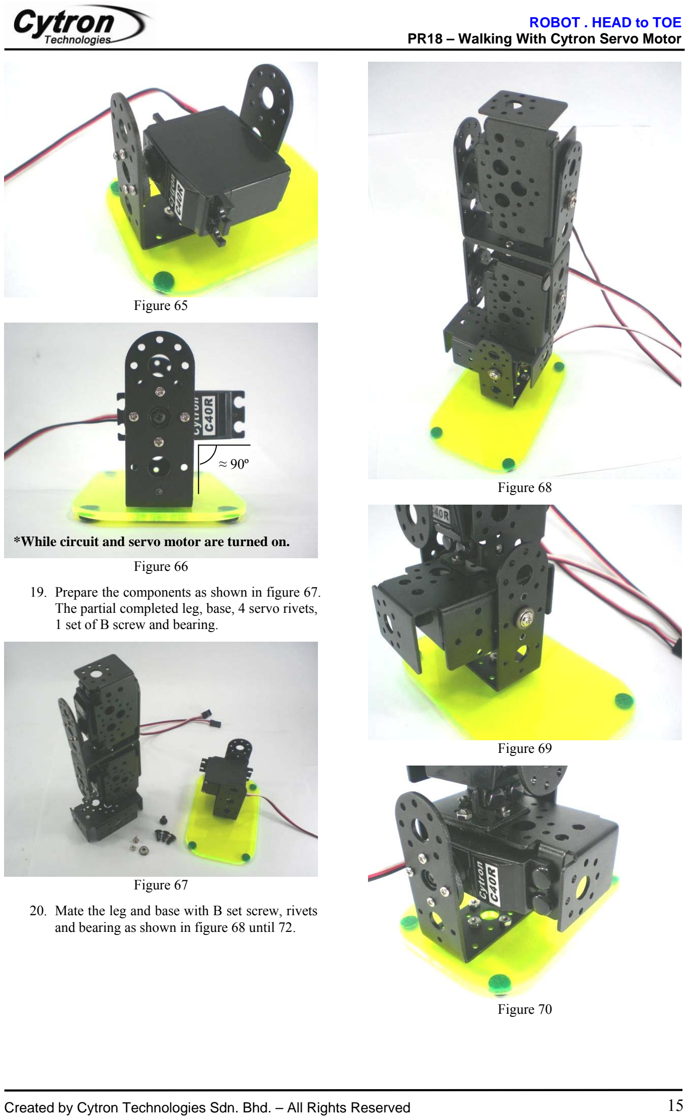
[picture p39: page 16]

Created by Cytron Technologies Sdn. Bhd. – All Rights Reserved | 15

Figure 65

Figure 66
19. Prepare the components as shown in figure 67. The partial completed leg, base, 4 servo rivets, 1 set of B screw and bearing.

Figure 67
20. Mate the leg and base with B set screw, rivets and bearing as shown in figure 68 until 72.

Figure 68

Figure 69

Figure 70

≈ 90º

*While circuit and servo motor are turned on.

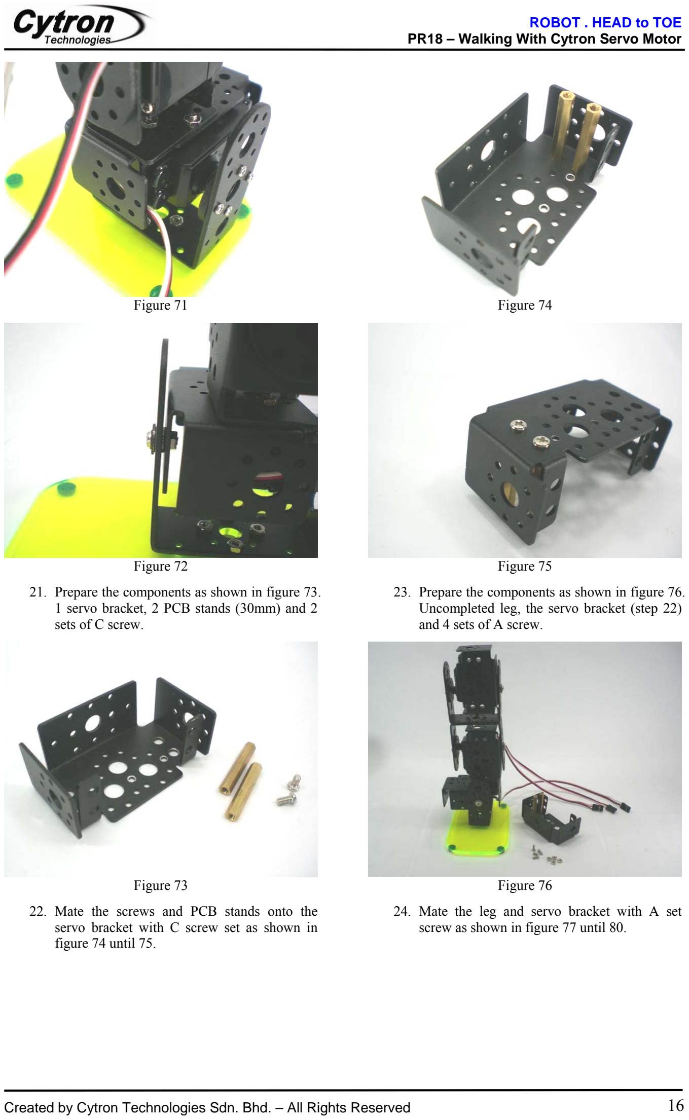
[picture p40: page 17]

Created by Cytron Technologies Sdn. Bhd. – All Rights Reserved | 16

Figure 71

Figure 72
21. Prepare the components as shown in figure 73. 1 servo bracket, 2 PCB stands (30mm) and 2 sets of C screw.

Figure 73
22. Mate the screws and PCB stands onto the servo bracket with C screw set as shown in figure 74 until 75.

Figure 74

Figure 75
23. Prepare the components as shown in figure 76. Uncompleted leg, the servo bracket (step 22) and 4 sets of A screw.

Figure 76
24. Mate the leg and servo bracket with A set screw as shown in figure 77 until 80.

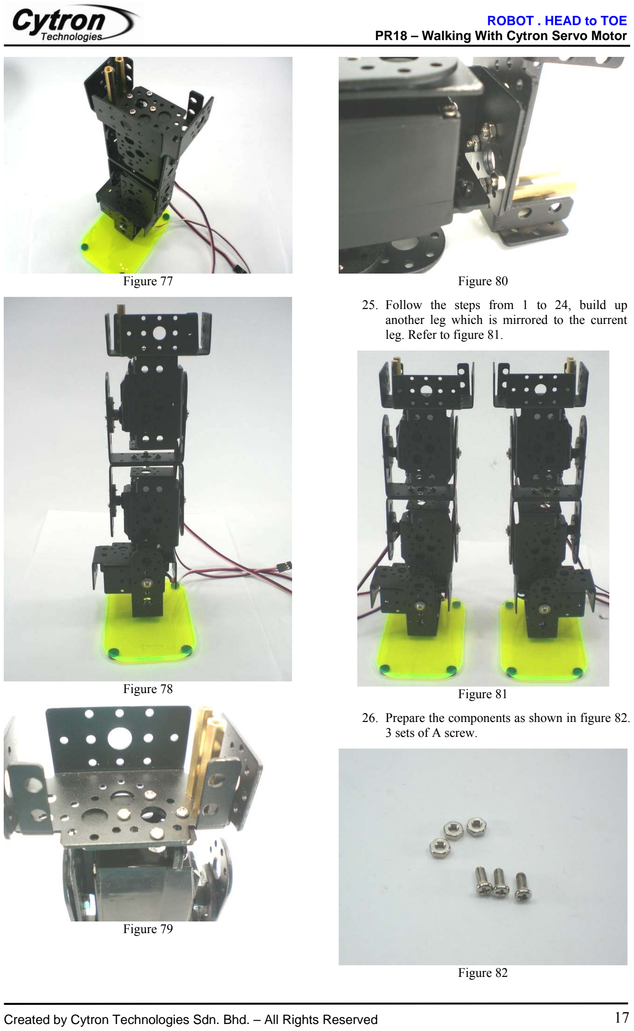
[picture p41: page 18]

Created by Cytron Technologies Sdn. Bhd. – All Rights Reserved | 17

Figure 77

Figure 78

Figure 79

Figure 80
25. Follow the steps from 1 to 24, build up another leg which is mirrored to the current leg. Refer to figure 81.

Figure 81
26. Prepare the components as shown in figure 82. 3 sets of A screw.

Figure 82

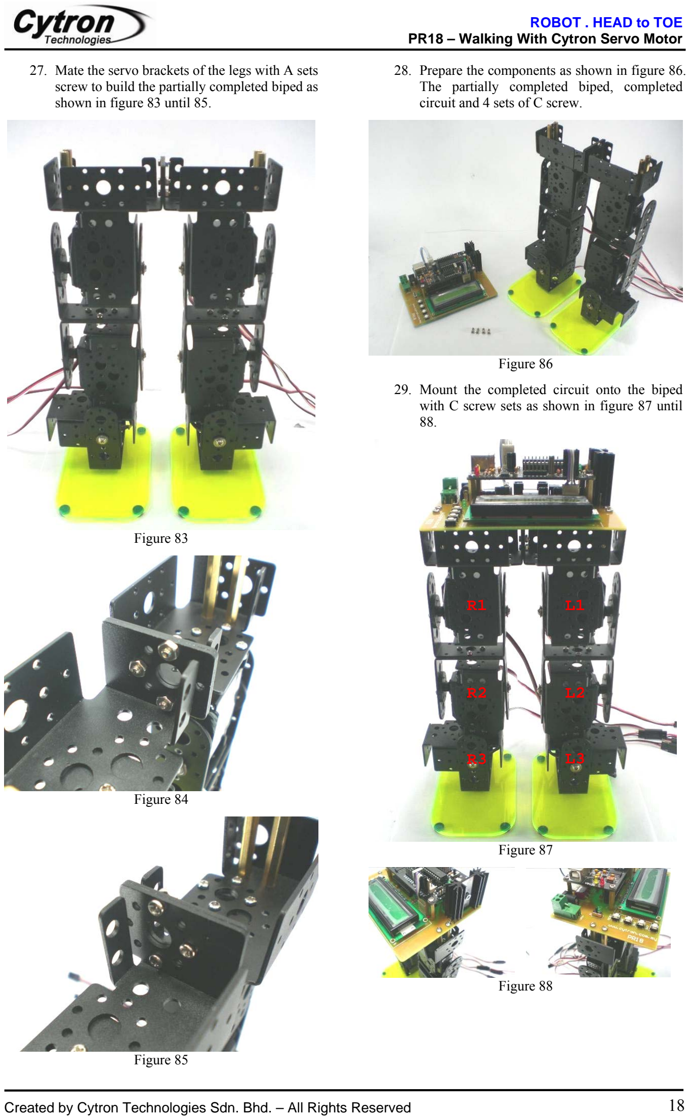
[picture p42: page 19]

Created by Cytron Technologies Sdn. Bhd. – All Rights Reserved | 18
27. Mate the servo brackets of the legs with A sets screw to build the partially completed biped as shown in figure 83 until 85.

Figure 83

Figure 84

Figure 85

28. Prepare the components as shown in figure 86. The partially completed biped, completed circuit and 4 sets of C screw.

Figure 86
29. Mount the completed circuit onto the biped with C screw sets as shown in figure 87 until 88.

Figure 87

Figure 88

L1

L2

R1

L3

R2

R3

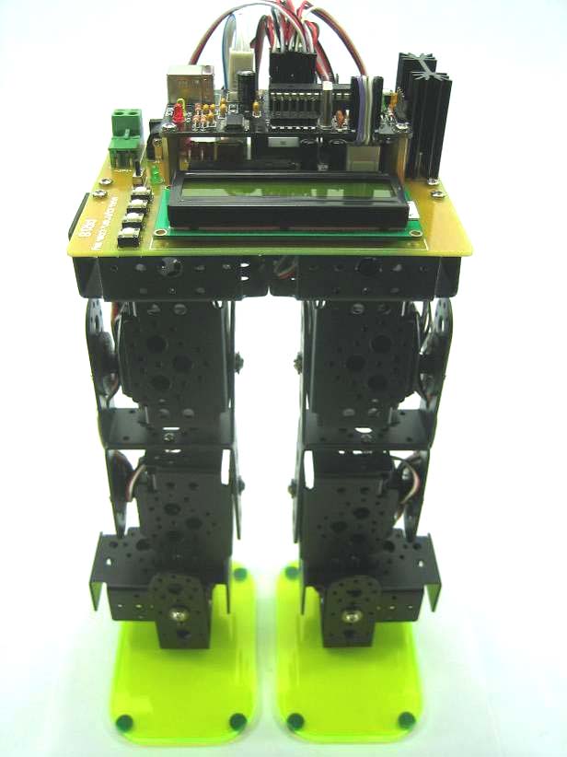
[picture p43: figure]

Created by Cytron Technologies Sdn. Bhd. – All Rights Reserved | 19
30. Connect the servo motors to the SC16A servo controller according to their respective channel. (L1 to channel S10, L2 to channel S11, L3 to channel S12, R1 to channel S7, R2 to channel S8, R3 to channel S9, refer to figure 15, figure 87 and figure 89). For L2, L3, R2 and R3, extension cables are needed to connect the motors to SC16A.

Figure 89
31. The completed biped is shown in figure 90.

Figure 90

### Calibrate the Servo Motor’s Position

The default values for every servo motors in the program are 732. As shown in figure, the default value does not represent the exact middle position. User has to tune it and modify the values in the program.
1. Turn on the circuit power and motor power, the servo motor is no exactly in the middle position as shown in figure 91.

Figure 91
2. Press the SW2 button of PR18 circuit board to increase the mode to “Calibration?” as shown in figure 92.

Figure 92
3. Press the SW3 button (OK) as shown in figure 93.

Figure 93

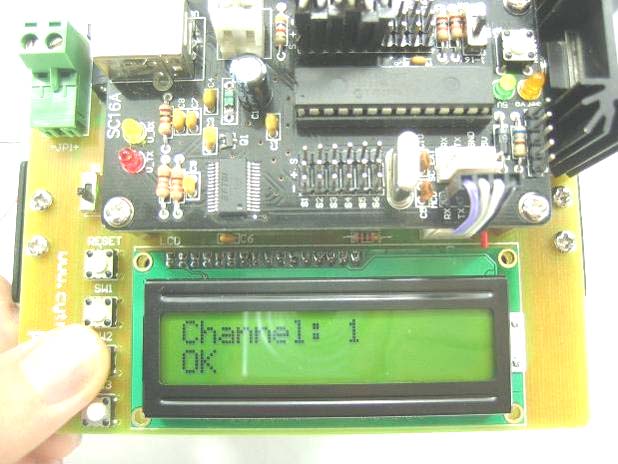
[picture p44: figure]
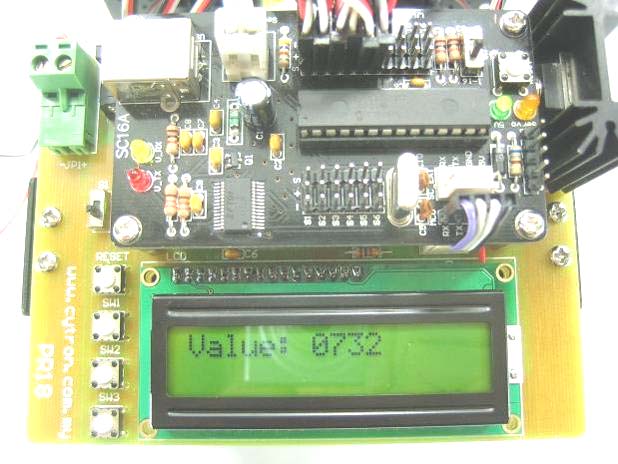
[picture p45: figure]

Created by Cytron Technologies Sdn. Bhd. – All Rights Reserved | 20
4. The number of channel will be display on the LCD as shown in figure. Press SW1/SW2 to decrease/increase the number of channel.

Figure 94

5. For this example, the servo L2 (S11) is being calibrated. Change the channel number to 11 and press SW3 button (OK) to proceed. The default value (732) of the current channel (S11) will be shown. Refer to figure 95 and figure 96.

Figure 95

Figure 96

6. Press SW1/SW2 to decrease/increase the value. For this example, the value (693) of the channel (L2, i.e. S11) brings the servo motor to its middle position. Refer figure 97 and figure 98.

Figure 97

Figure 98
7. The steps are same for the base of the biped. As shown in figure 99, the positions of the base servo motor (L3, i.e. S12) before and after calibration.
Before | After
Figure 99

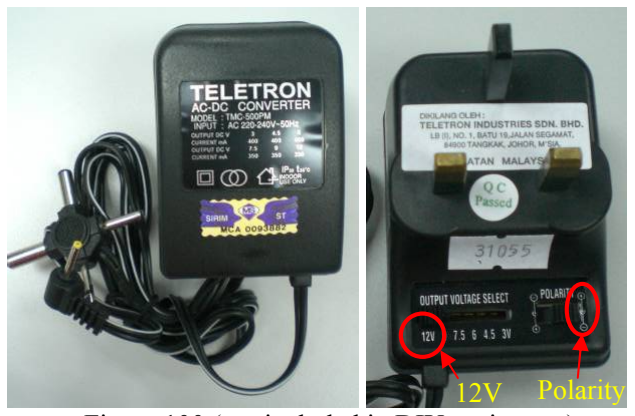
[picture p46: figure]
12V Polarity

Created by Cytron Technologies Sdn. Bhd. – All Rights Reserved | 21
8. Modify the corresponding value of mid_Lx and mid_Rx (x = 1, 2 or 3) for the servo motors. This new value should be placed in the C source code file. Refer to figure 15 under SOFTWARE. Compile it and reload it to the PR18 board.

### AC to DC adaptor:

User can decide either uses a 12V battery or an AC to DC adaptor as the power source to the circuit. The picture and the way to use the adaptor are shown in Figure 11 and 12. However, as discussed in earlier section, normal AC to DC adaptor is not sufficient to supply current to whole biped servo motor. Thus, user is advice to use SLA (Sealed Lead Acid), Lipo (Lithium-Polymer) or other powerful battery to power up this project.

Figure 100 (not included in DIY project set)

Figure 101
After connecting the power supply to the completed biped, user can execute the first mode “Biped Walking?” to perform a biped walking. User can also modify the program to test the functionality of the biped. Have fun!

### WARRANTY

No warranty will be provided as this is DIY project. Please check the polarity of each electronic component before soldering it to board.

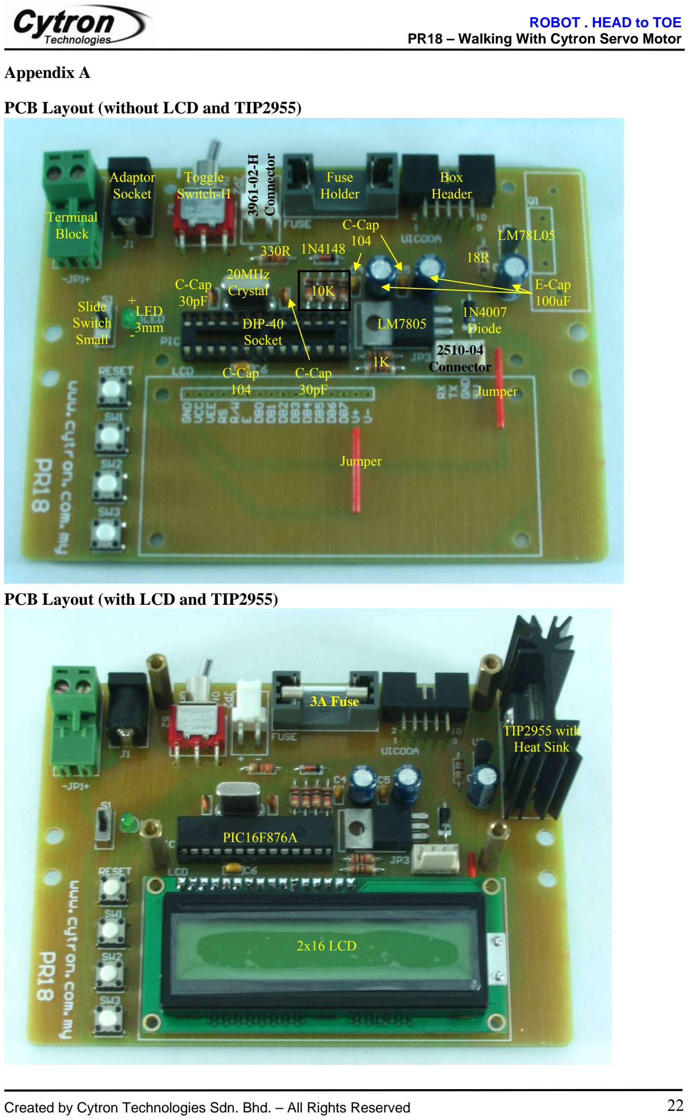
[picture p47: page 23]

Created by Cytron Technologies Sdn. Bhd. – All Rights Reserved | 22

### Appendix A

### PCB Layout (without LCD and TIP2955)

### PCB Layout (with LCD and TIP2955)

Terminal
Block

DIP-40
Socket

20MHz
Crystal

C-Cap
30pF

C-Cap
30pF

Fuse
Holder

Box
Header

Toggle
Switch-H

3961-02-H

Connector
Adaptor
Socket

18R

10K
1N4007
Diode LM7805

LM78L05

C-Cap
104

C-Cap
104

1K

+

330R 1N4148

E-Cap
100uF

2510-04
Connector

Jumper

Jumper

Slide
Switch
Small

3A Fuse

PIC16F876A

TIP2955 with
Heat Sink

2x16 LCD

LED
3mm

Created by Cytron Technologies Sdn. Bhd. – All Rights Reserved | 1

### PCB Layout (Completed with SC16A)

* Cytron Technologies reserved the right to replace the component in the list with component of the same functionality without prior notice.

### Prepared by

Cytron Technologies Sdn. Bhd. 19, Jalan Kebudayaan 1A,
Taman Universiti,
81300 Skudai,
Johor, Malaysia.

### Tel: +607-521 3178 Fax: +607-521 1861

### URL: www.cytron.com.my Email: support@cytron.com.my

| sales@cytron.com.my
